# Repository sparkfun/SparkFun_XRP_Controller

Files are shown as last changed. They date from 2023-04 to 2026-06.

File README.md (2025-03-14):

SparkFun XRP Controller
========================================

<table>
    <tr>
        <td></td>
        <td></td>
    </tr>
    <tr>
        <th style="text-align: center;"><a href="https://www.sparkfun.com/sparkfun-experiential-robotics-platform-xrp-controller.html"><i>SparkFun XRP Controller</i></a></th>
        <th style="text-align: center;"><a href="https://www.sparkfun.com/sparkfun-experiential-robotics-platform-xrp-controller-beta.html"><i>SparkFun XRP Controller - Beta</i></a></th>
    </tr>
</table>

The Experiential Robotics Platform (XRP) Controller and Experiential Robotics Platform (XRP) Controller - Beta operate as the "brains" of the Experiential Robotics Platform Kits. These boards provide the programming and operation interface to connect and control the motors, sensors and other peripherals included in the XRP Kits. The controller boards primary microcontrollers are a Pico W (XRP-Beta) and RP2350 (XRP) and also include motor drivers, 6 DoF IMU, motor and sensor connectors along with other user interfaces.

Repository Contents
-------------------

* **/Documents** - Data sheets, additional product information
* **/Hardware** - Eagle design files (.brd, .sch)
* **/Production** - Production panel files (.brd)
* **/docs** - GitHub Pages documentation files (.md, images)

Documentation
--------------

* **[Hardware Overview](https://docs.sparkfun.com/SparkFun_XRP_Controller/introduction/)** - Basic hardware overview for the XRP Controller - Beta and XRP Controller.
* **[Experiential Robotics Platform Org](https://experientialrobotics.org/)** - Experiential Robotics Platform homepage.

Product Versions
----------------

* [ROB-22727](https://www.sparkfun.com/sparkfun-experiential-robotics-platform-xrp-controller-beta.html) - XRP Controller - Beta
* [ROB-26619](https://www.sparkfun.com/sparkfun-experiential-robotics-platform-xrp-controller.html) - XRP Controller

License Information
-------------------

This product is ***open source***!

Please review the LICENSE.md file for license information.

If you have any questions or concerns on licensing, please contact technical support on our [SparkFun forums](https://forum.sparkfun.com/viewforum.php?f=152).

Distributed as-is; no warranty is given.

* Your friends at SparkFun.

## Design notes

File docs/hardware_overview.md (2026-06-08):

In this document, we'll take a close look at the heart of the Experiential Robotics Platform (XRP) Kit, the XRP Controller. This document outlines all of the parts on this board you'll interact with while building and using the XRP Kit.

## Controller Board Overview

Let's take a broad look at the major components on the XRP Controller. The photo below points them out along with their names:

<figure markdown>
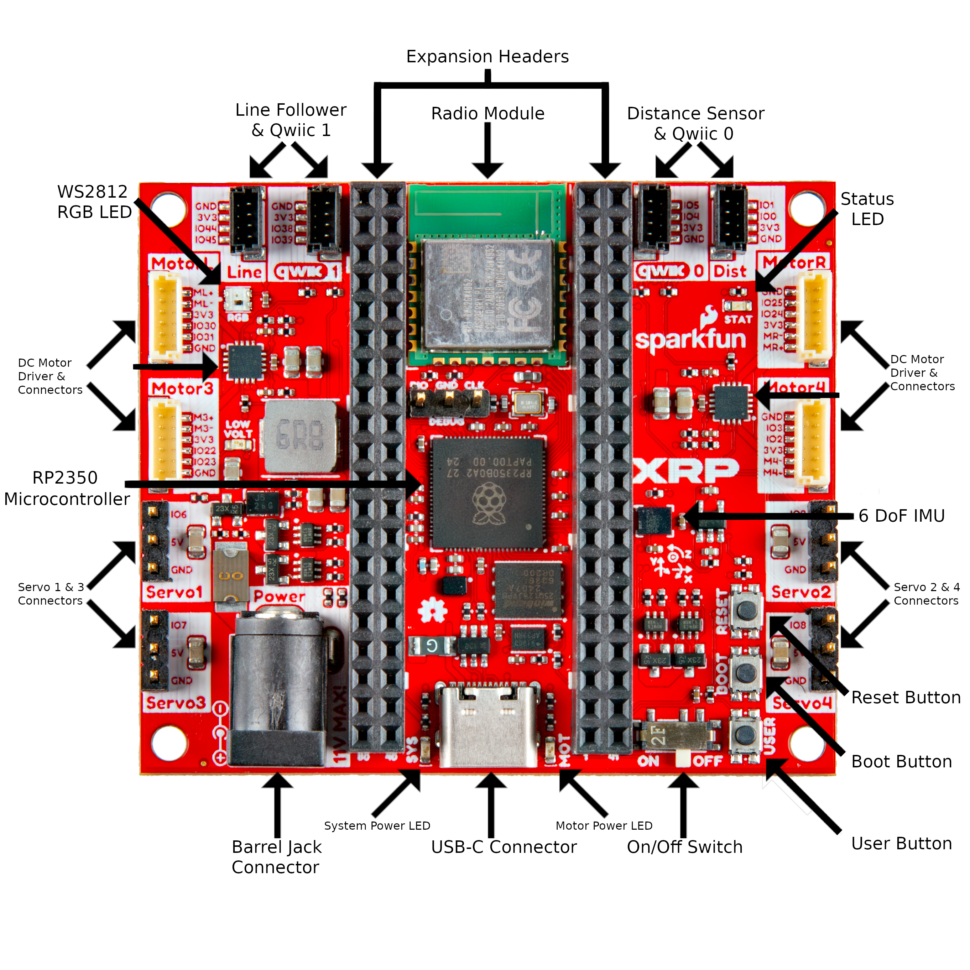
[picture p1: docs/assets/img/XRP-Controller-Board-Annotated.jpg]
Overview photo labeling the major components and other hardware on the XRP Controller Board

<figcaption>Having trouble seeing the detail in the image? Click on it for a larger view.</figcaption>
</figure>

You'll notice that along with the arrows showing the name of some of the smaller components, the board uses what's called silkscreen to label all the connectors, buttons, LEDs and other parts you'll interact with while building and using the XRP Robotics Kit.

## Raspberry Pi RP2350 & Radio Module 2

The Raspberry Pi RP2350 acts as the brain of this board. The RP2350 communicates with the motor controllers, IMU and other components to control the robotics kit's behavior. The Raspberry Pi Radio Module 2 (RM2) adds wireless connectivity to the XRP Controller over both WiFi and Bluetooth<sup>&reg;</sup>. The photo below highlights the RP2350 and RM2 on the Controller Board:

<figure markdown>
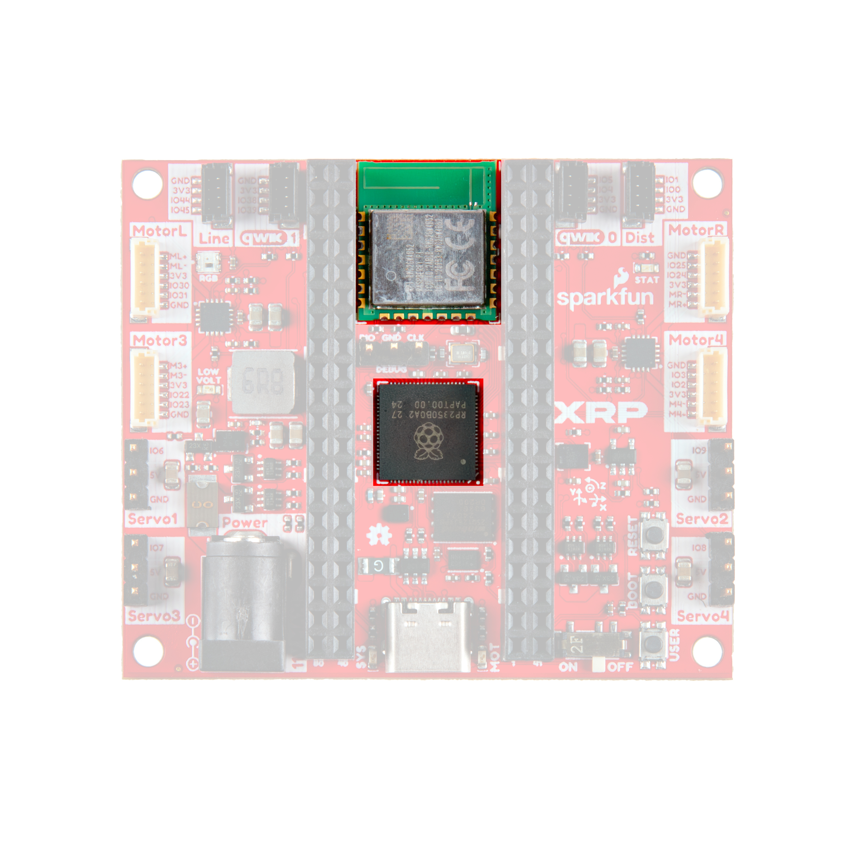
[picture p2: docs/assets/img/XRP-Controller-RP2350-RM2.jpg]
Photo highlighting the RP2350 IC

</figure>

Think of the RP2350 as a brain sending signals to other parts of the "body" to tell them what to do. It has several General Purpose Input/Output (GPIO) pins that connect to the other major parts on this board so it can send and receive data from them and return it to you visually (such as seeing the motors move) or virtually (such as watching data on a computer monitor). 

The Radio Module 2 connects to both WiFi networks and Bluetooth devices allowing wireless connectivity for the XRP Kit. It communicates with the RP2350 over its serial peripheral interface (SPI) and also has a few general purpose inputs and outputs (GPIO) that are connected to the two 2x20 expansion headers on the XRP Controller Board. 

## DRV8411A Motor Drivers

The pair of DRV8411A H-Bridge motor drivers from Texas Instruments<sup>&trade;</sup> on the XRP Controller Board control the direction and speed of the XRP Kit's motors.

<figure markdown>
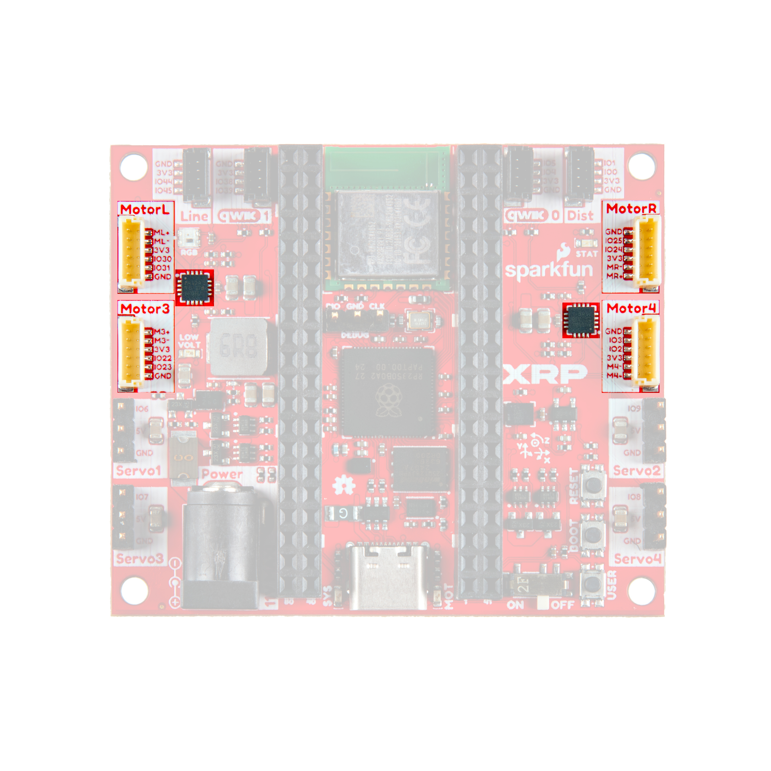
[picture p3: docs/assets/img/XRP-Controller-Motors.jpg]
Photo highlighting the motor drivers.

</figure>

The term H-bridge comes from how this circuit design looks on a schematic diagram. It has four internal switches that control whether the motor spins Clockwise (CW), Counter Clockwise (CCW), Coasts (no drive power), and Stops. When going through the XRP Kit curriculum you'll learn how to program the robot to tell the motor drivers to control the motors' speed and direction.  

## LSM6DSO 6-Dof IMU

The LSM6DSO 6-DoF (Degrees of Freedom) IMU (Inertial Measurement Unit) from STMicroelectronics<sup>&trade;</sup> combines an accelerometer and gyroscope into a single IC (integrated circuit). This sensor lets you measure the robot's acceleration in three dimensions and also measure the orientation and angle of the robot. 

<figure markdown>
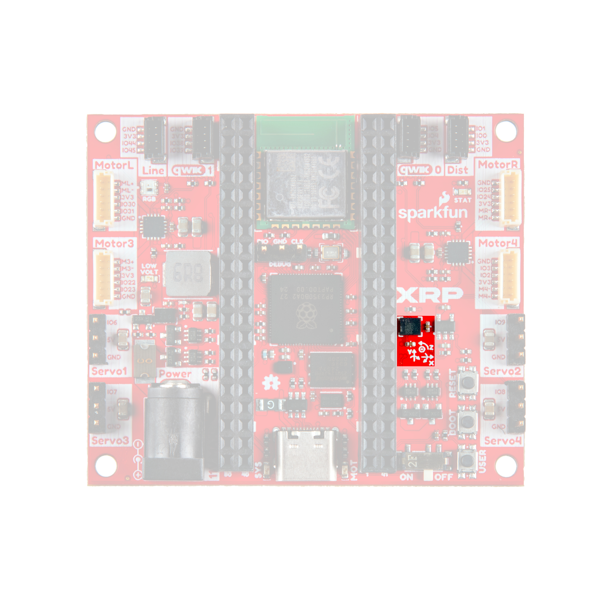
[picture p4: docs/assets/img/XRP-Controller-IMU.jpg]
Photo highlighting the 6 DoF IMU.

</figure>

The accelerometer in this chip has four measurement ranges of &plusmn;2/&plusmn;4/&plusmn;8/&plusmn;16 g. These ranges allow you to customize the limits of the acceleration forces measured. The gyroscope has five selectable measurement ranges of &plusmn;125/&plusmn;250/&plusmn;500/&plusmn;1000/&plusmn;2000 DPS (degrees per second). Refer to the silk screen symbols on the XRP Controller for the directions of each axis.

## Power Components

Now let's take a closer look at the parts on this board used for providing power to it.

<figure markdown>
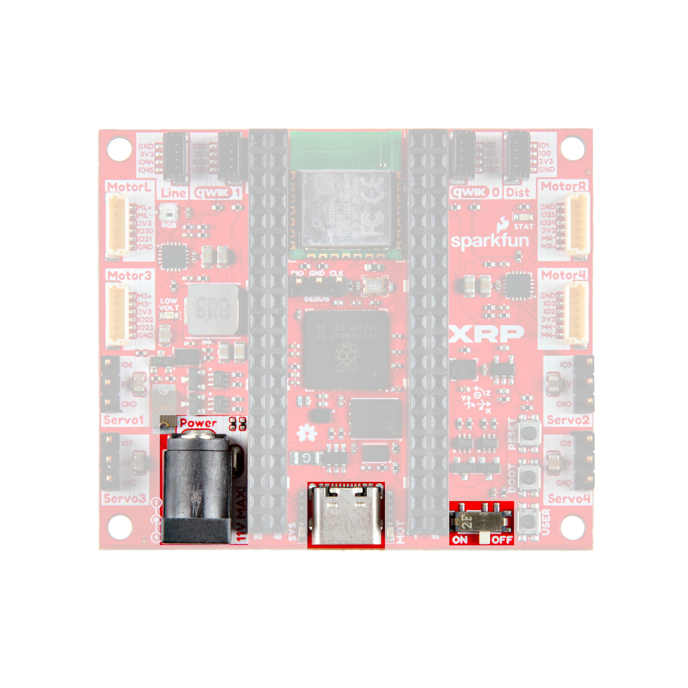
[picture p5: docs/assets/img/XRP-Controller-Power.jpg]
Photo highlighting the power components.

</figure>

### Barrel Jack Connector

The barrel jack connector is the primary power input for the entire XRP Kit. This connector mates with the cable from the XRP Kit's battery pack for battery-powered operation. Take note that the maximum safe voltage that can be applied to this connector is <b>11V</b> and the minimum recommended voltage to run the system is <b>4.8V</b> so you can use non-alkaline batteries like NiMH cells. The 4-AA battery pack included with the kit supplies a maximum of <b>6V</b> so most users will have no issues exceeding the max voltage.

### USB-C Connector

The USB-C connector provides power to the XRP Controller Board with <b>5V</b> from a USB cable. It also is the primary interface you'll use to initially set up the XRP Controller Board with a computer and program the RP2350 using a USB-C cable.

### Power Switch

The power switch highlighted above controls the voltage input to the Controller Board. This two-way switch turns the kit's power on and off. You can use this to turn the robot off while keeping the battery pack plugged in. The switch does not affect the RP2350's power when a USB cable is plugged in.

## Motor Connectors

The Controller Board has four six-pin connectors labeled <b>Motor L</b>, <b>Motor R</b>, <b>Motor 3</b> and <b>Motor 4</b> and four three-pin connectors labeled <b>Servo 1</b>, <b>Servo 2</b>, <b>Servo 3</b> and <b>Servo 4</b>. 

<figure markdown>
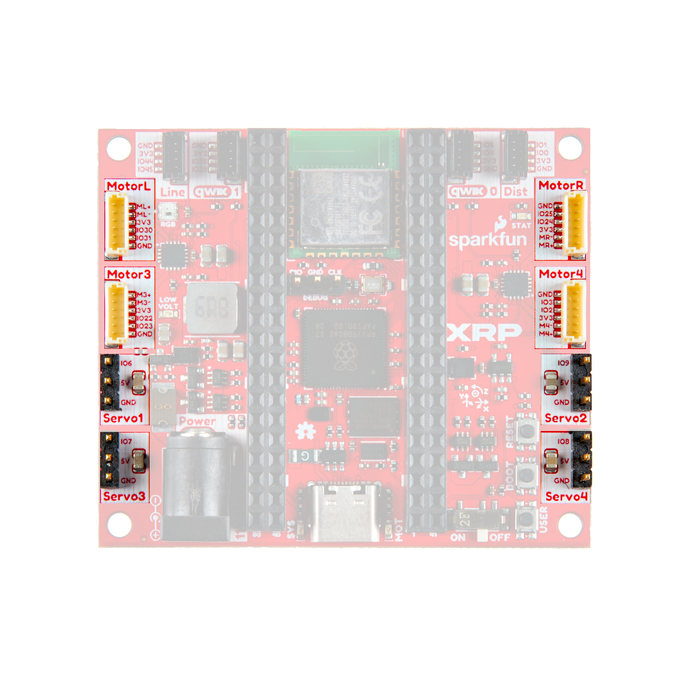
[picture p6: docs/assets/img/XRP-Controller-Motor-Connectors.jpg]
Photo highlighting the motor connectors.

</figure>

### DC Motor Connectors

The DC Motor connectors are where you'll plug in the left and right motors while assembling the kit. These connectors include the power connections for the motor as well as the encoders on the motors. The board routes these connections through the motor drivers to GPIO pins on the RP2350. You'll use these pins to monitor how many rotations the motor completes and use that data to determine how far the robot has traveled. Refer to the Pinout table at the end of this document for the specific GPIO pins each motor connects to on the RP2350. The Controller Board has two extra motor connectors for expansion projects using more than two motors.

### Servo Motor Connectors

The four three-pin connectors on either side of the board labeled Servo 1, Servo 2, Servo 3 and Servo 4 mate with servo motors. You'll use the Servo 2 connector to hook up the servo included in the XRP kit. The other three connectors are extra for expansion projects. These connectors have power pins (<b>5V</b> and Ground) and a signal pin to control the motion of the servo motor. Servo motors use a communication method called pulse width modulation (PWM) that tells the motor to move and with some motors, where to move to. If you're interested in learning more about how servo motors work, you may want to check out SparkFun's [Servos Explained](https://www.sparkfun.com/servos) page for information and tutorials on how to use them.

## Sensor & Qwiic Connectors

The Controller Board has four four-pin connectors labeled (from left to right when looking at the labels upright) <b>Line</b>, <b>Qwiic 1</b>, <b>Qwiic 0</b> and <b>DIST</b>. Their labels indicate their use as well as which GPIO pins they connect to on the RP2350. These connectors provide an easy plug-in connection for the line follower and distance sensor as well as two extra connectors for expansion projects. These connectors are polarized meaning they only work when connected properly but they are keyed and there is only one way to plug a cable into them.

<figure markdown>
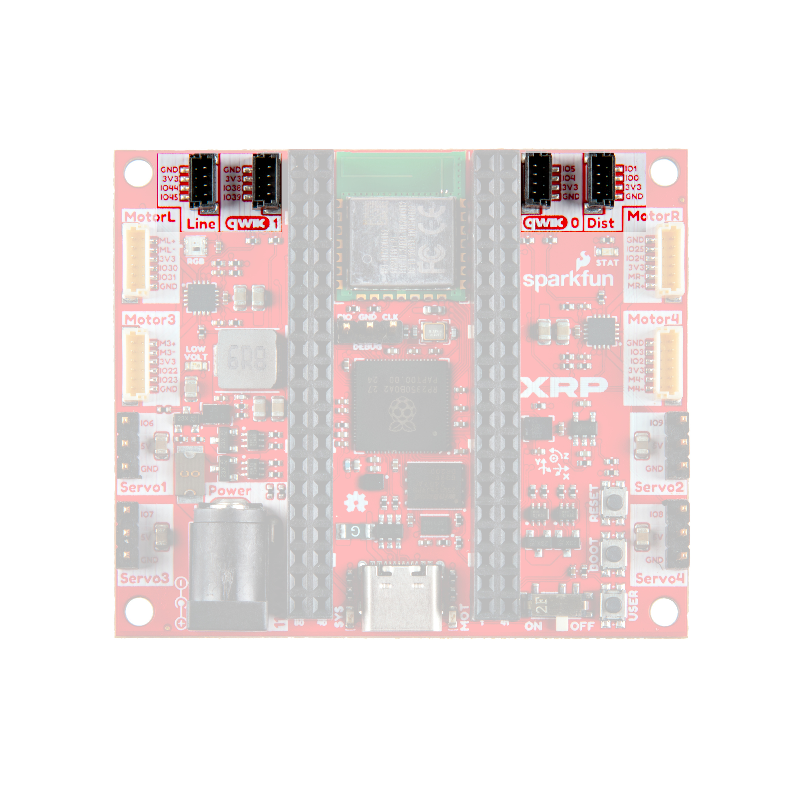
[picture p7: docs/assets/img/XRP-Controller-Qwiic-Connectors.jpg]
Photo highlighting Qwiic and expansion connectors

</figure>

### Line Follower Connector

The Line connector is where you'll plug the cable for the line follower sensor into. This connects the sensor's two signal lines, Left and Right, to the RP2350's GPIO44 (Left) and GPIO45 (Right) pins. You'll use these pins to monitor whenever the sensor detects the robot has gone past the left or right threshold when performing line-following experiments. When connecting the Qwiic adapter cable that plugs into this connector, make the following connections to the Line Follower Sensor:

* **Red** - **3.3V**
* **Blue** - **S1**
* **Yellow** - **S2**
* **Black** - **GND**

### Distance Sensor Connector

The Dist connector is where you'll plug the cable for the ultrasonic range sensor into. It connects the distance sensor's Echo and Trigger lines to the RP2350's GPIO0 (Trigger) and GPIO1 (Echo). You'll use these pins to receive distance data from the ultrasonic range sensor. When connecting the Qwiic adapter cable that plugs into this connector, make the following connections to the Distance Sensor:

* **Red** - **VCC**
* **Blue** - **Trig**
* **Yellow** - **Echo**
* **Black** - **GND**

### Qwiic Connectors

The Qwiic connectors work with SparkFun's [Qwiic ecosystem](https://www.sparkfun.com/qwiic) of sensors that communicate over I<sup>2</sup>C. This is a two-wire communication protocol that works with a large variety of sensors and other electronics. With this, you can customize the XRP Kit to add things like environmental sensing, OLED screens, data logging, and more!

## Buttons

The Controller Board has three push buttons labeled <b>USER</b>, <b>RESET</b> and <b>BOOT</b> (on the RP2350). 

<figure markdown>
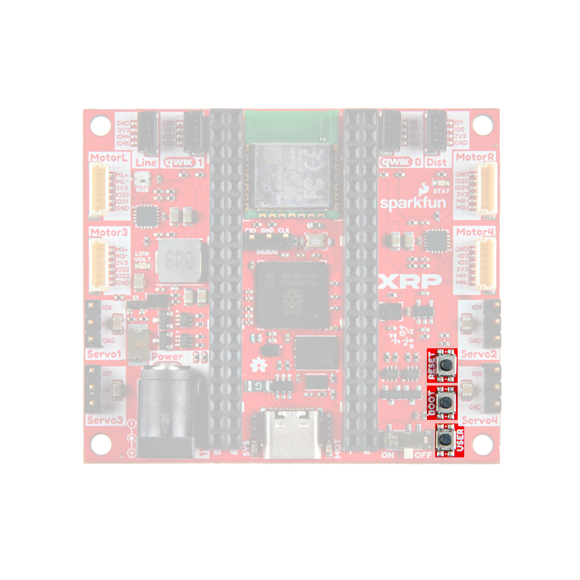
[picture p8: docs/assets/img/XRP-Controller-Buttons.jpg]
Photo highlighting buttons.

</figure>

The USER button connects to GPIO36 on the RP2350 which allows it to be programmed for various purposes. The RESET button does just what its name suggests and resets the entire board when pressed. This can help to reboot the robot or to restart a sequence you want the Robotics Kit to perform. Holding the BOOT button either when plugging in a USB cable or when pressing the RESET button sets the RP2350 to behave as a mass storage device when connected to a computer for uploading firmware. 

## LEDs

There are five LEDs on the XRP Controller Board labeled <b>MOT</b>, <b>SYS</b>, <b>LOW VOLT</b>, <b>STAT</b> and <b>RGB</b>. 

<figure markdown>
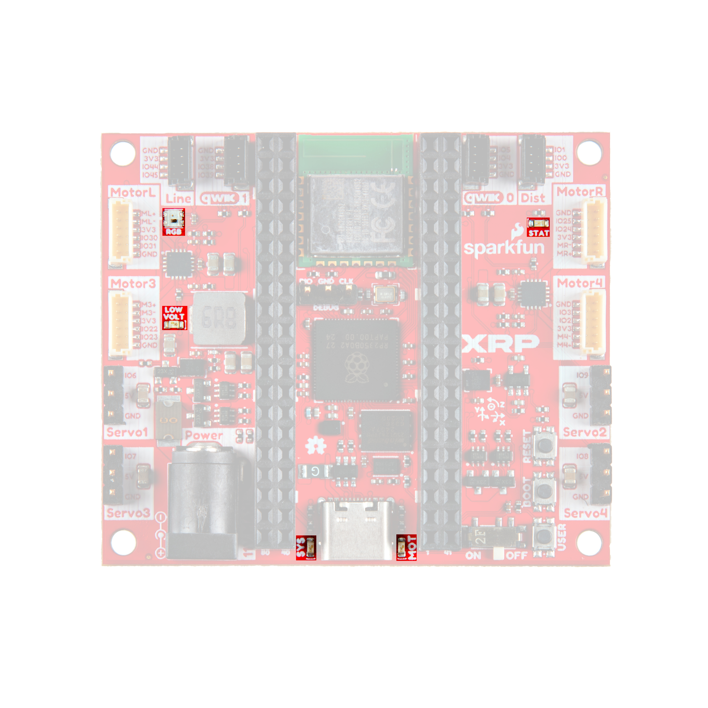
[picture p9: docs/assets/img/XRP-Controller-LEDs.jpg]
Photo highlighting LEDs

</figure>

These LEDs are there to provide a visual indication to users. The LEDs labeled <b>MOT</b> and <b>SYS</b> turn on when their respective power rails are powered. The <b>MOT</b> LED turns on when the motors have power available. The <b>SYS</b> LED turns on when the <b>3.3V</b>/System circuit is powered. This circuit powers the RP2350, RM2, sensors, and the expansion connectors. The <b>LOW VOLT</b> LED connects to the 5V Buck regulator POWER_GOOD pin. It provides a quick visual indicator to notify users that the supply voltage has dropped below the operating threshold and the board is underpowered. This is <b>not</b> technically a low battery indicator but it coincidentally starts illuminating when 4xAA batterys are low, depending on the battery chemistry. 

The other two LEDs labeled <b>STAT</b> and <b>RGB</b> are user-programmable status LEDs you can program for whatever behavior you prefer. The <b>STAT</b> LED connects to GPIO0 on the Radio Module and can be useful to indicate behavior from the radio such as connection status or data transmission. The <b>RGB</b> LED connects to GPIO37 on the RP2350 and can be programmed to change to any color based on whatever behavior you'd like. For example, you can have it turn from Green to Red when the distance sensor detects the robot is nearing an obstacle. 

## Expansion Headers

The XRP Controller Board now features a pair of 2x20 female headers that connect to nearly all the RP2350's and RM2's available pins to allow for more customization options for the XRP platform. Many of these pins are shared between the connectors and other components on the XRP Control Board so take care to ensure they are not being used by any peripherals (motors, sensors, etc.) before connecting and programming them for a different functionality.

<figure markdown>
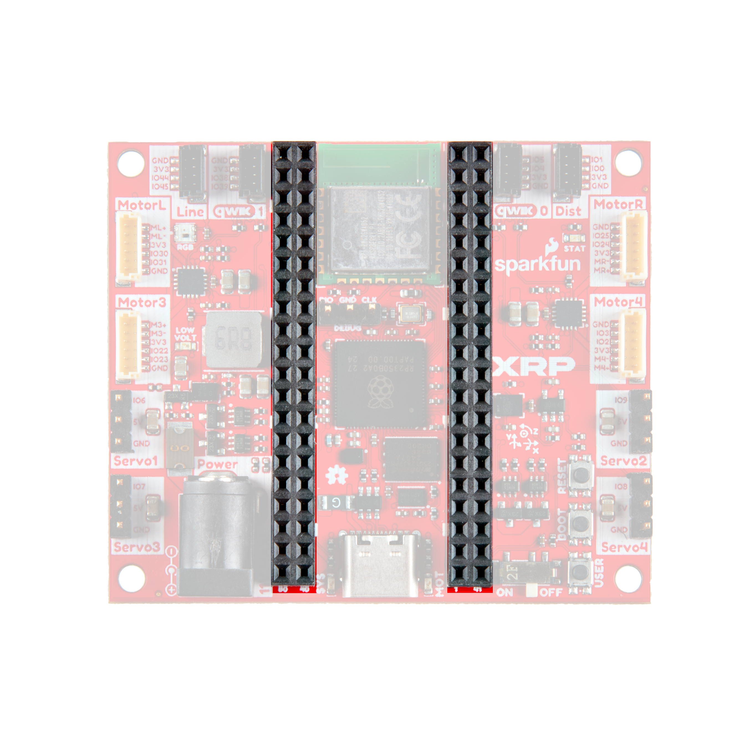
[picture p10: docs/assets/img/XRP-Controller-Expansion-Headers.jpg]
Photo highlighting 2x20 expansion headers.

</figure>

The inner rows of this expansion header nearly matches the pinout of the Pico W 2 (minus the analog-to-digital conversion pins) and can be used with peripheral boards that work with the Pico 2 W. Please note this is <b>NOT</b> a socket for a Pico 2 W. The outer row contains available GPIO pins from the RM2, extra GPIO pins from the RP2350 along with voltage pins. The image below and following table offers a quick reference for the pinout and labels on the expansion headers as well as any other connectors (motors, sensors, etc.) or peripheral (button, LED, etc.) shared between them.

<figure markdown>
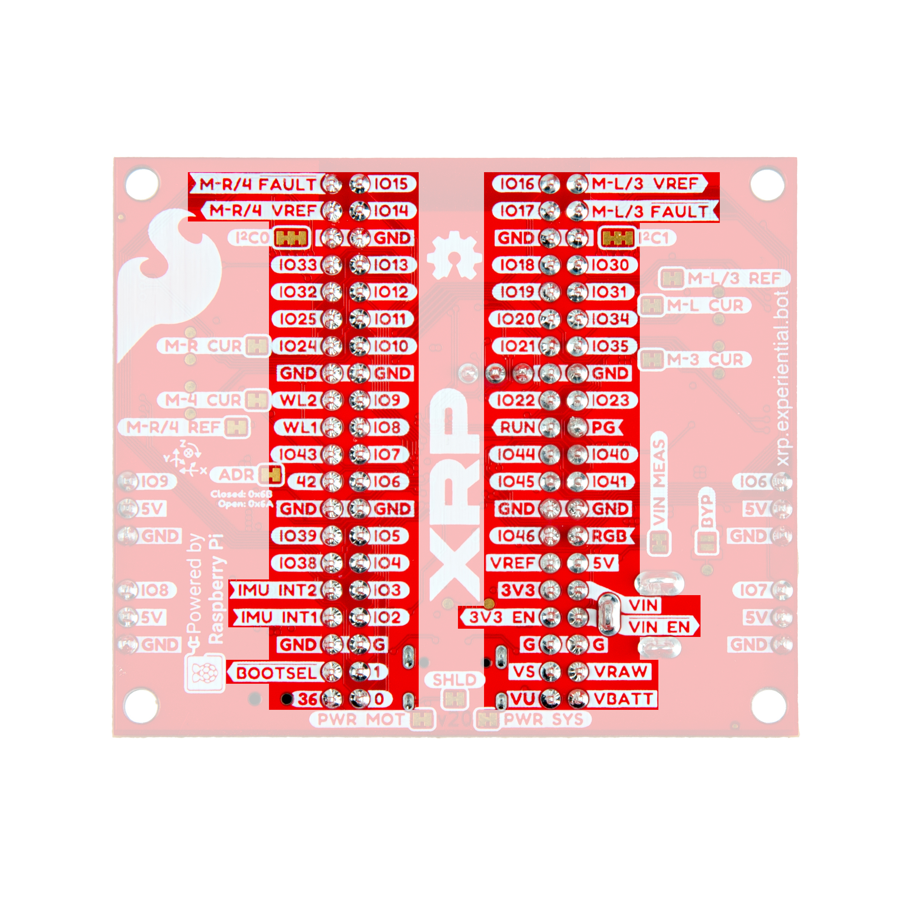
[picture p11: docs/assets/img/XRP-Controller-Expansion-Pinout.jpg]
Photo highlighting pin labels on the XRP Controller board.

</figure> 

<figure markdown>
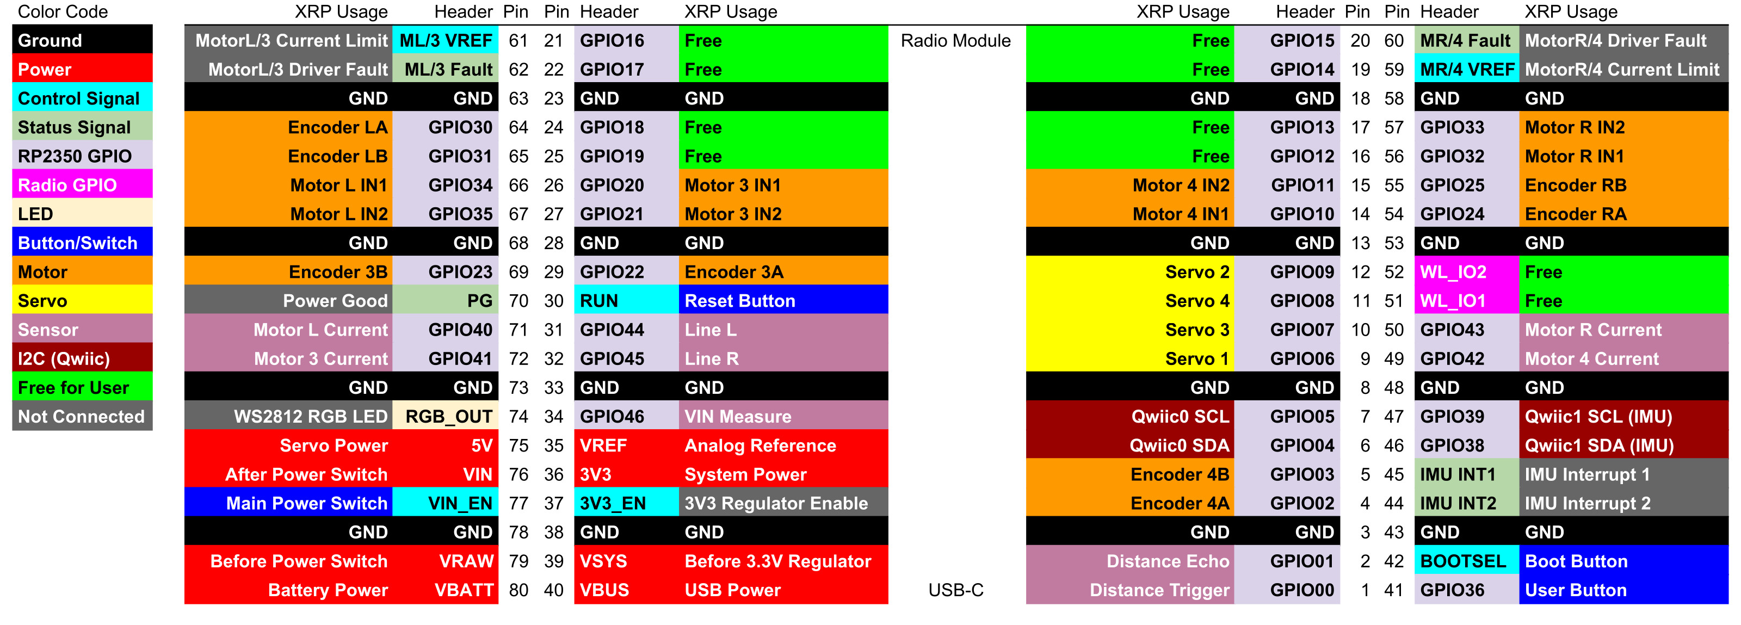
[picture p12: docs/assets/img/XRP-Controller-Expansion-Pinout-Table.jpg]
Table of expansion header pinout

</figure>

## Solder Jumpers

!!! warning Advanced Users Only

    These solder jumpers can change the behavior of the board in a lasting way. Using these requires extra tools not included in the XRP
     Kit along with knowledge of how to use and interact with solder jumpers. We recommend that only advanced users adjust and change the solder jumpers. If you'd like to learn more about how to use solder jumpers, check out SparkFun's [How to Work with Jumper Pads and PCB Traces](https://learn.sparkfun.com/tutorials/how-to-work-with-jumper-pads-and-pcb-traces) tutorial.

The XRP Controller Board has fourteen solder jumpers. A solder jumper provides a customization option for advanced users to control the behavior of the pins and components they connect to. The solder jumpers on this board are labeled (from top-to-bottom reading left-to-right when looking at the photo below): <b>I<sup>2</sup>C0</b>, <b>I<sup>2</sup>C1</b>, <b>M-L/3 REF</b>, <b>M-L CUR</b>, <b>M-R CUR</b>, <b>M-3 CUR</b>, <b>M-4 CUR</b>, <b>M-R/4 REF</b> <b>ADR</b>, <b>VIN MEAS</b>, <b>BYPM</b>, <b>SHLD</b>, <b>PWR MOT</b> and <b>PWR SYS</b>. 

<figure markdown>
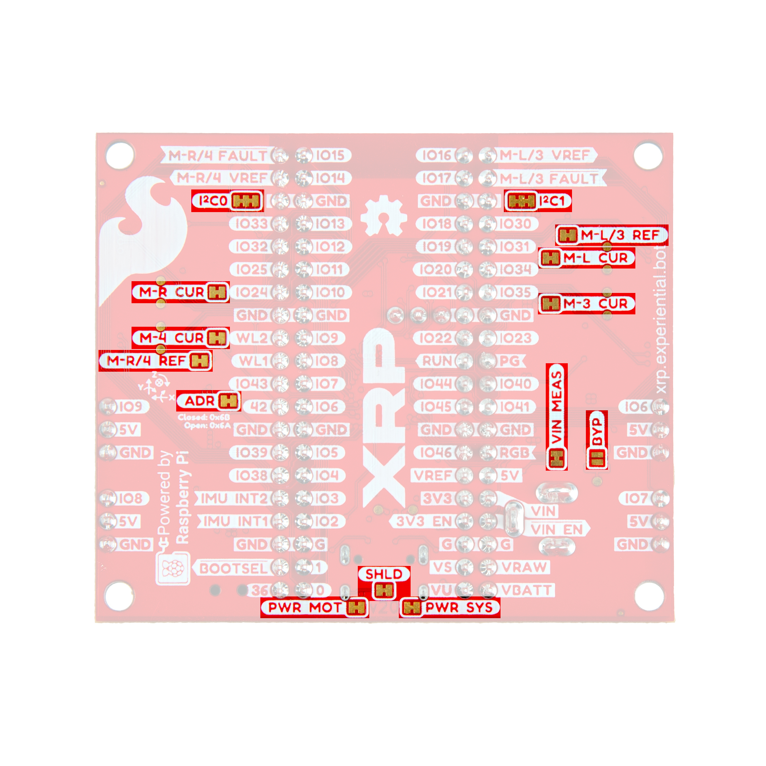
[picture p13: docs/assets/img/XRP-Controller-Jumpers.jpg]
Photo highlighting solder jumpers.

</figure>

<table>
    <tr>
        <th>Label</th>
        <th>Default State</th>
        <th>Function</th>
        <th>Notes</th>
    </tr>
    <tr>
        <td>I<sup>2</sup>C0</td>
        <td>CLOSED</td>
        <td>Pulls SDA/SCL on I<sup>2</sup>C 0 to <b>3.3V</b> through two <b>2.2k&ohm;</b> resistors.</td>
        <td>Open completely to disable the pull up resistors on the I<sup>2</sup>C 0 bus.</td>
    </tr>
    <tr>
        <td>I<sup>2</sup>C1</td>
        <td>CLOSED</td>
        <td>Pulls SDA/SCL on I<sup>2</sup>C 0 to <b>3.3V</b> through two <b>2.2k&ohm;</b> resistors.</td>
        <td>Open completely to disable the pull up resistors on the I<sup>2</sup>C 1 bus.</td>
    </tr>
    <tr>
        <td>M-L/3 REF</td>
        <td>CLOSED</td>
        <td>Sets the Left/3 DRV8411 motor driver's voltage reference to <b>3.3V</b.</td>
        <td>Sets the DRV8411's reference voltage to match the system voltage. Open to set to a different voltage.</td>
    </tr>
    <tr>
        <td>M-L CUR</td>
        <td>CLOSED</td>
        <td>Connects the Left Motor current sense output to IO40.</td>
        <td>Lets users measure motor current draw using the ADC on IO40. Open to free up IO40 for other use.</td>
    </tr>
    <tr>
        <td>M-R CUR</td>
        <td>CLOSED</td>
        <td>Connects the Right Motor current sense output to IO43.</td>
        <td>Lets users measure motor current draw using the ADC on IO43. Open to free up IO43 for other use.</td>
    </tr>
    <tr>
        <td>M-3 CUR</td>
        <td>CLOSED</td>
        <td>Connects the Motor Three current senss output to IO41.</td>
        <td>Lets users measure motor current draw using the ADC on IO41. Open to free up IO41 for other use.</td>
    </tr>
    <tr>
        <td>M-4 CUR</td>
        <td>CLOSED</td>
        <td>Connects the Motor Four current sense output to IO42.</td>
        <td>Lets users measure motor current draw using the ADC on IO42. Open to free up IO42 for other use.</td>
    </tr>
    <tr>
        <td>M-R/4 REF</td>
        <td>CLOSED</td>
        <td>Sets the Right/4 DRV8411 motor driver's voltage reference to <b>3.3V</b.</td>
        <td>This sets the DRV8411's reference voltage to match the system voltage. Open to set to a different voltage.</td>
    </tr>
    <tr>
        <td>ADR</td>
        <td>CLOSED</td>
        <td>Sets the LSM6DSO's I<sup>2</sup>C address to <b>0x6B</b>.</td>
        <td>Open to switch the I<sup>2</sup>C address to <b>0x6A</b>.</td>
    </tr>
    <tr>
        <td>VIN MEAS</td>
        <td>CLOSED</td>
        <td>Connects the VIN measurement circuit to IO46</td>
        <td>Open to free up IO46 for alternate use</td>
    </tr>
    <tr>
        <td>BYP</td>
        <td>OPEN</td>
        <td>Enables the fuse for the barrel jack input.</td>
        <td>Close to bypass the fuse for the barrel jack.</td>
    </tr>
    <tr>
        <td>SHLD</td>
        <td>CLOSED</td>
        <td>Connects the USB-C shield pin to the board's ground plane.</td>
        <td>Open to isolate the USB-C shield pin</td>
    </tr>
    <tr>
        <td>PWR MOT</td>
        <td>CLOSED</td>
        <td>Completes the Motor Power LED circuit.</td>
        <td>Open to disable the Motor Power LED.</td>
    </tr>
    <tr>
        <td>PWR SYS</td>
        <td>CLOSED</td>
        <td>Completes the System Power LED circuit.</td>
        <td>Open to disable the System Power LED.</td>
    </tr>
</table>

## Pinout Reference Table

The table below gives a quick reference for the complete pinout of the XRP Controller and which pins they connect to on the RP2350.

<table>
    <tr>
        <th>RP2350 GPIO Pin</th>
        <th>Connector/Peripheral Label</th>
        <th>Expansion Header Pin Label</th>
        <th>Pin Function</th>
    </tr>
    <tr>
        <td>GPIO0</td>
        <td>DIST</td>
        <td>0</td>
        <td>Distance Trigger Pin</td>
    </tr>
    <tr>
        <td>GPIO1</td>
        <td>DIST</td>
        <td>1</td>
        <td>Distance Echo Pin</td>
    </tr>
    <tr>
        <td>GPIO2</td>
        <td>Motor 4</td>
        <td>IO2</td>
        <td>Motor 4 Encoder A</td>
    </tr>
    <tr>
        <td>GPIO3</td>
        <td>Motor 4</td>
        <td>IO3</td>
        <td>Motor 4 Encoder B</td>
    </tr>
    <tr>
        <td>GPIO4</td>
        <td>Qwiic 0</td>
        <td>IO4</td>
        <td>I<sup>2</sup>C 0 Data Signal</td>
    </tr>
    <tr>
        <td>GPIO5</td>
        <td>Qwiic 0</td>
        <td>IO5</td>
        <td>I<sup>2</sup>C 0 Clock</td>
    </tr>
    <tr>
        <td>GPIO6</td>
        <td>Servo 1</td>
        <td>IO6</td>
        <td>Servo 1 Signal</td>
    </tr>
    <tr>
        <td>GPIO7</td>
        <td>Servo 3</td>
        <td>IO7</td>
        <td>Servo 3 Signal</td>
    </tr>
    <tr>
        <td>GPIO8</td>
        <td>Servo 4</td>
        <td>IO8</td>
        <td>Servo 4 Signal</td>
    </tr>
    <tr>
        <td>GPIO9</td>
        <td>Servo 2</td>
        <td>IO9</td>
        <td>Servo 2 Signal</td>
    </tr>
    <tr>
        <td>GPIO10</td>
        <td>Motor 4</td>
        <td>IO10</td>
        <td>Motor 4 Phase Pin</td>
    </tr>
    <tr>
        <td>GPIO11</td>
        <td>Motor 4</td>
        <td>IO11</td>
        <td>Motor 4 Enable Pin</td>
    </tr>
    <tr>
        <td>GPIO12</td>
        <td>None</td>
        <td>IO12</td>
        <td>Available I/O</td>
    </tr>
    <tr>
        <td>GPIO13</td>
        <td>None</td>
        <td>IO13</td>
        <td>Available I/O</td>
    </tr>
    <tr>
        <td>GPIO14</td>
        <td>None</td>
        <td>IO14</td>
        <td>Available I/O</td>
    </tr>
    <tr>
        <td>GPIO15</td>
        <td>None</td>
        <td>IO15</td>
        <td>Available I/O</td>
    </tr>
    <tr>
        <td>GPIO16</td>
        <td>None</td>
        <td>IO16</td>
        <td>Available I/O</td>
    </tr>
    <tr>
        <td>GPIO17</td>
        <td>None</td>
        <td>IO17</td>
        <td>Available I/O</td>
    </tr>
    <tr>
        <td>GPIO18</td>
        <td>None</td>
        <td>IO18</td>
        <td>Available I/O</td>
    </tr>
    <tr>
        <td>GPIO19</td>
        <td>None</td>
        <td>IO19</td>
        <td>Available I/O</td>
    </tr>
    <tr>
        <td>GPIO20</td>
        <td>Motor 3</td>
        <td>IO20</td>
        <td>Motor 3 Phase Pin</td>
    </tr>
    <tr>
        <td>GPIO21</td>
        <td>Motor 3</td>
        <td>IO21</td>
        <td>Motor 3 Enable Pin</td>
    </tr>
    <tr>
        <td>GPIO22</td>
        <td>Motor 3</td>
        <td>IO22</td>
        <td>Motor 3 Encoder A Pin</td>
    </tr>
    <tr>
        <td>GPIO23</td>
        <td>Motor 3</td>
        <td>IO23</td>
        <td>Motor 3 Encoder B Pin</td>
    </tr>
    <tr>
        <td>GPIO24</td>
        <td>Motor R</td>
        <td>IO24</td>
        <td>Motor R Encoder A Pin</td>
    </tr>
    <tr>
        <td>GPIO25</td>
        <td>Motor R</td>
        <td>IO25</td>
        <td>Motor R Encoder B Pin</td>
    </tr>
    <tr>
        <td>GPIO26</td>
        <td>None</td>
        <td>None</td>
        <td>RM2 Power On</td>
    </tr>
        <td>GPIO27</td>
        <td>None</td>
        <td>None</td>
        <td>RM2 Chip Select</td>
    </tr>
    </tr>
        <td>GPIO28</td>
        <td>None</td>
        <td>None</td>
        <td>RM2 SPI Clock</td>
    </tr>
    </tr>
        <td>GPIO29</td>
        <td>None</td>
        <td>None</td>
        <td>RM2 SPI Data</td>
    </tr>
    <tr>
        <td>GPIO30</td>
        <td>Motor L</td>
        <td>IO30</td>
        <td>Motor L Encoder A Pin</td>
    </tr>
    <tr>
        <td>GPIO31</td>
        <td>Motor L</td>
        <td>IO31</td>
        <td>Motor L Encoder B Pin</td>
    </tr>
    <tr>
        <td>GPIO32</td>
        <td>Motor R</td>
        <td>IO32</td>
        <td>Motor R Phase Pin</td>
    </tr>
    <tr>
        <td>GPIO33</td>
        <td>Motor R</td>
        <td>IO33</td>
        <td>Motor R Enable Pin</td>
    </tr>
    <tr>
        <td>GPIO34</td>
        <td>Motor L</td>
        <td>IO34</td>
        <td>Motor L Phase Pin</td>
    </tr>
    <tr>
        <td>GPIO35</td>
        <td>Motor L</td>
        <td>IO35</td>
        <td>Motor L Enable Pin</td>
    <tr>
    <tr>
        <td>GPIO36</td>
        <td>User Button</td>
        <td>36</td>
        <td>User button input</td>
    </tr>
    <tr>
        <td>GPIO37</td>
        <td>RGB</td>
        <td>RGB</td>
        <td>WS2812 Data In Pin</td>
    </tr>
    <tr>
        <td>GPIO38</td>
        <td>Qwiic 1</td>
        <td>SDA1</td>
        <td>I<sup>2</sup>C 1 Data</td>
    </tr>
    <tr>
        <td>GPIO39</td>
        <td>Qwiic 1</td>
        <td>SCL1</td>
        <td>I<sup>2</sup>C 1 Clock</td>
    </tr>
    <tr>
        <td>GPIO40</td>
        <td>None</td>
        <td>IO40</td>
        <td>Motor Left Current Measure</td>
    </tr>
    <tr>
        <td>GPIO41</td>
        <td>None</td>
        <td>IO41</td>
        <td>Motor 3 Current Measure</td>
    </tr>
    <tr>
        <td>GPIO42</td>
        <td>None</td>
        <td>IO42</td>
        <td>Motor 4 Current Measure</td>
    </tr>
    <tr>
        <td>GPIO43</td>
        <td>None</td>
        <td>IO43</td>
        <td>Motor Right Current Measure</td>
    </tr>
    <tr>
        <td>GPIO44</td>
        <td>Line</td>
        <td>IO44</td>
        <td>Line Follower Left Signal</td>
    </tr>
    <tr>
        <td>GPIO45</td>
        <td>Line</td>
        <td>IO45</td>
        <td>Line Follower Right Signal</td>
    </tr>
    <tr>
        <td>GPIO46</td>
        <td>None</td>
        <td>IO46</td>
        <td>Voltage Input Measure</td>
    </tr>
    <tr>
        <td>GPIO47</td>
        <td>None</td>
        <td>None</td>
        <td>PSRAM Chip Select</td>
    </tr>
</table>

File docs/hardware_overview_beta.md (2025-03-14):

In this document, we'll take a close look at the heart of the Experiential Robotics Platform (XRP) Kit - Beta, the XRP Controller - Beta. This document outlines all of the parts on this board you'll interact with while building and using the XRP Kit - Beta.

## XRP Controller - Beta Overview

Let's take a broad look at the major components on the XRP Controller - Beta. The photo below points them out along with their names:

<figure markdown>
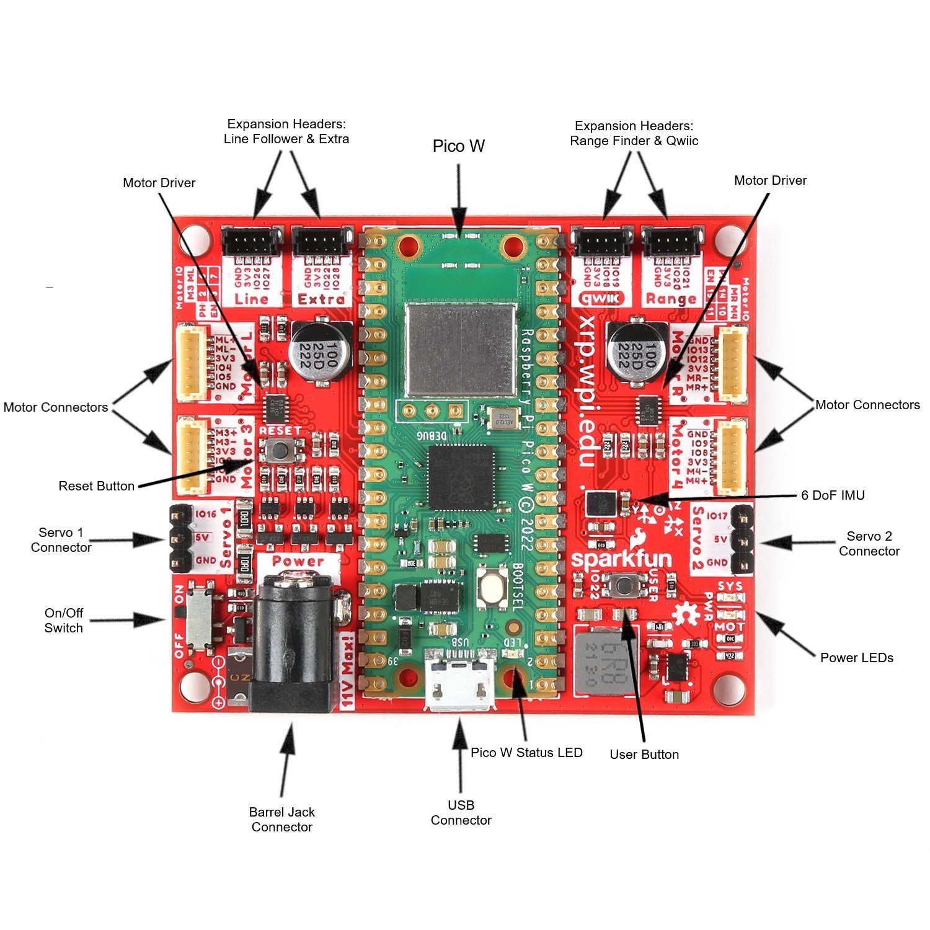
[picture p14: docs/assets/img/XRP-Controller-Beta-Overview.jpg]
Overview photo labeling the major components and other hardware on the XRP Controller - Beta

<figcaption>Having trouble seeing the detail in the image? Click on it for a larger view.</figcaption>
</figure>

You'll notice that along with the arrows showing the name of some of the smaller components, the board uses what's called silkscreen to label all the connectors, buttons, LEDs and other parts you'll interact with while building and using the XRP Kit - Beta.

## Raspberry Pi Pico W

The Raspberry Pi Pico W microcontroller acts as the brain of this board. It combines a RP2040 processor with a wireless module for both 2.4GHz 802.11n wireless LAN and Bluetooth<sup>&trade;</sup> 5.2. The RP2040 communicates with the motor controllers, IMU and other components to control the robotics kit's behavior. The photo below highlights the Pico W on the Controller board:

<figure markdown>
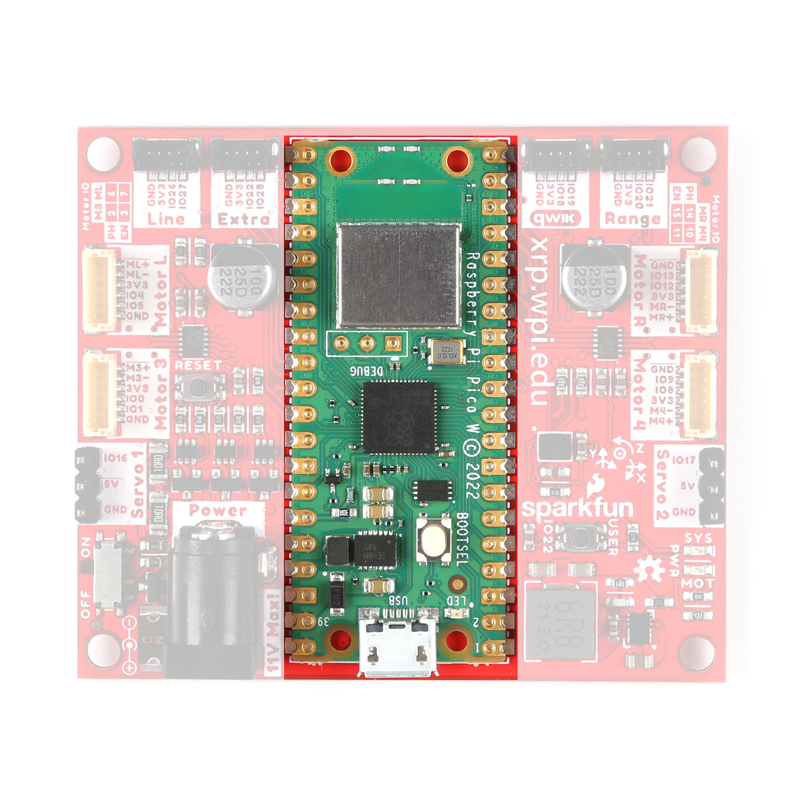
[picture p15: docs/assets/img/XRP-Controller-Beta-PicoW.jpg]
Photo highlighting the Pico W microcontroller

</figure>

Think of the Pico W as a brain sending signals to other parts of the "body" to tell them what to do. It has several General Purpose Input/Output (GPIO) pins that connect to the other major parts on this board so it can send and receive data from them and return it to you visually (such as seeing the motors move) or virtually (such as watching data on a computer monitor). 

## DRV8835 Motor Drivers

The pair of DRV8835 H-Bridge motor drivers from Texas Instruments<sup>&trade;</sup> on the XRP Controller - Beta control the direction and speed of the Robotics Kit's motors.

<figure markdown>
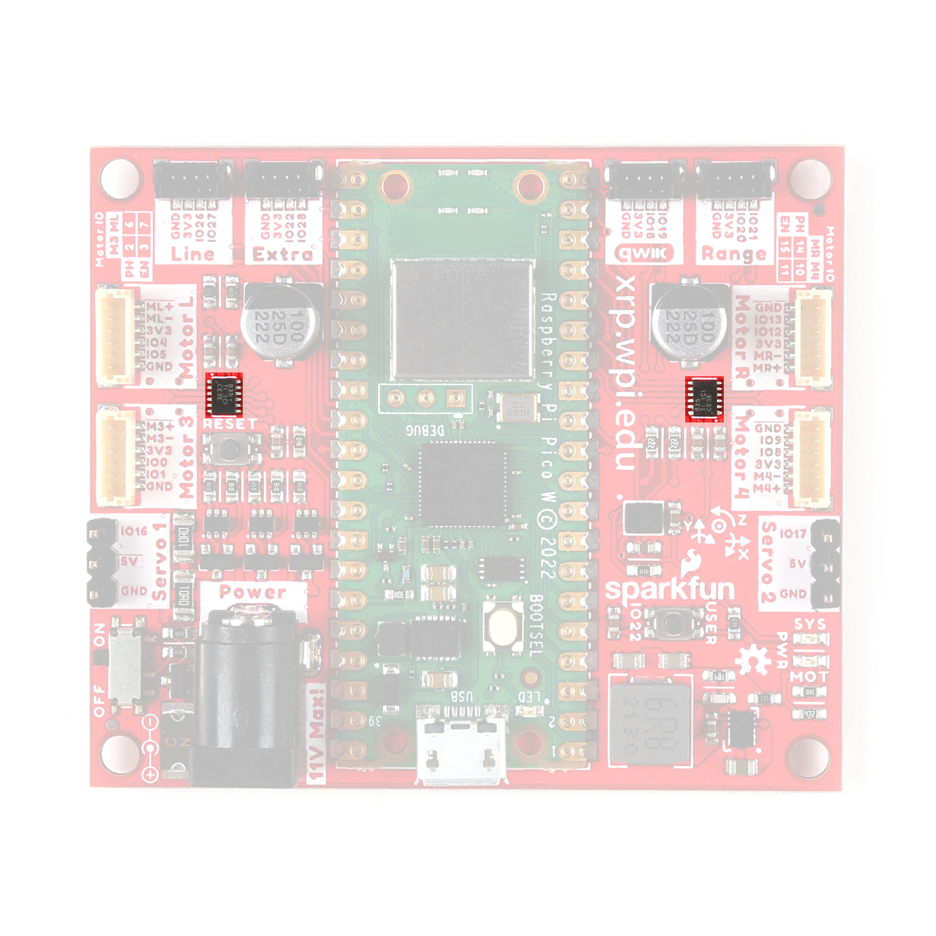
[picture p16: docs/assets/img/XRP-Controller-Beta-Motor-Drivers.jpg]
Photo highlighting the motor drivers.

</figure>

The term H-bridge comes from how this circuit design looks on a schematic diagram. It has four internal switches that control whether the motor spins Clockwise (CW), Counter Clockwise (CCW), Coasts (no drive power), and Stops. When going through the XRP Kit - Beta curriculum you'll learn how to program the robot to tell the motor drivers to control the motors' speed and direction.  

## LSM6DSO 6-Dof IMU

The LSM6DSO 6-DoF (Degrees of Freedom) IMU (Inertial Measurement Unit) from STMicroelectronics<sup>&trade;</sup> combines an accelerometer and gyroscope into a single IC (integrated circuit). This sensor lets you measure the robot's acceleration in three dimensions and also measure the orientation and angle of the robot. 

<figure markdown>
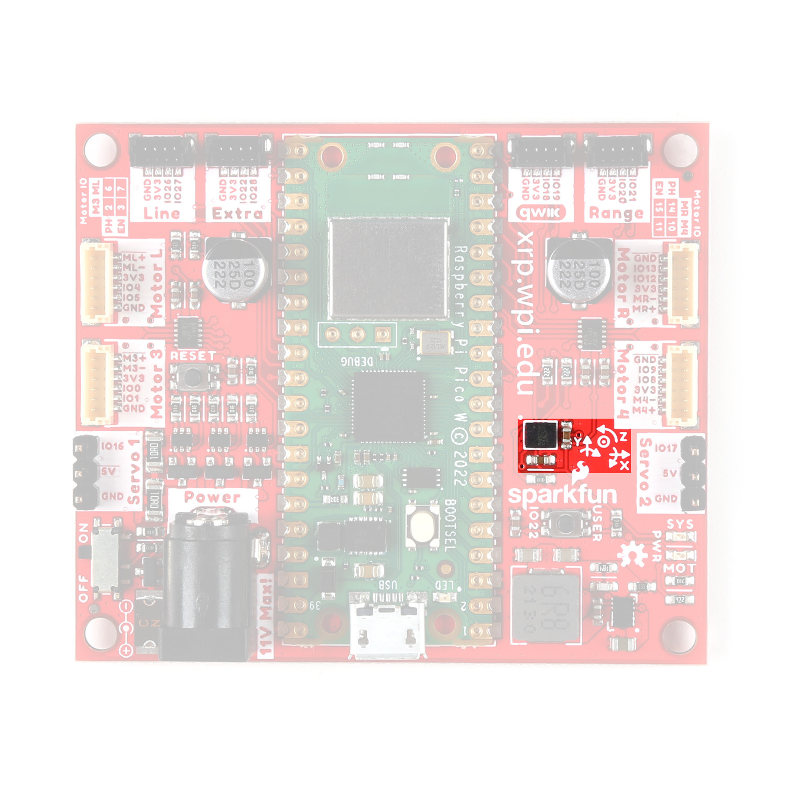
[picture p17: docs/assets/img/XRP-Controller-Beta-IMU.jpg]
Photo highlighting the 6 DoF IMU.

</figure>

The accelerometer in this chip has four measurement ranges of &plusmn;2/&plusmn;4/&plusmn;8/&plusmn;16 g. These ranges allow you to customize the limits of the acceleration forces measured. The gyroscope has five selectable measurement ranges of &plusmn;125/&plusmn;250/&plusmn;500/&plusmn;1000/&plusmn;2000 DPS (degrees per second).

## Power Components

Now let's take a closer look at the parts on this board used for providing power to it.

<figure markdown>
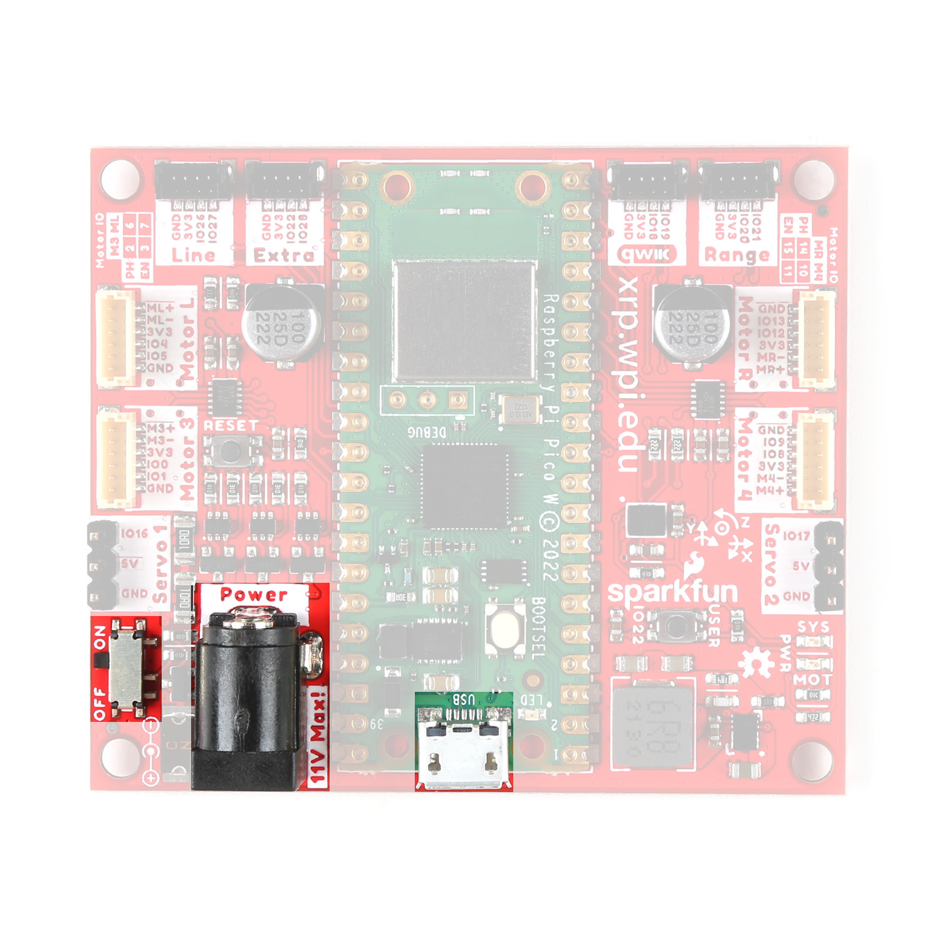
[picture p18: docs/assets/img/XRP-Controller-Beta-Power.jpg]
Photo highlighting the power components.

</figure>

### Barrel Jack Connector

The barrel jack connector is the primary power input for the entire XRP Kit - Beta. This connector mates with the cable from the XRP Kit - Beta's battery pack for battery-powered operation. Take note that the maximum safe voltage that can be applied to this connector is <b>11V</b> and the minimum to run the system is <b>5V</b>. The 4-AA battery pack included with the kit supplies a maximum of <b>6V</b> so most users will have no issues exceeding the max voltage.

### Pico W USB-Connector

The Pico W has a Micro-USB connector that can be used to power the controller board with <b>5V</b> from a USB cable. It also is the primary interface you'll use to initially set up the Pico W with a computer and program the Pico W over a USB cable.

### Power Switch

The power switch highlighted above controls the voltage input to the controller Board. This two-way switch turns the kit's power on and off. You can use this to turn the robot off while keeping the battery pack plugged in. The switch does not affect the Pico W's power when a USB cable is plugged in.

## Motor Connectors

The controller board has four six-pin connectors labeled <b>Motor L</b>, <b>Motor R</b>, <b>Motor 3</b>, and <b>Motor 4</b> and two three-pin connectors labeled <b>Servo 1</b> and <b>Servo 2</b>. 

<figure markdown>
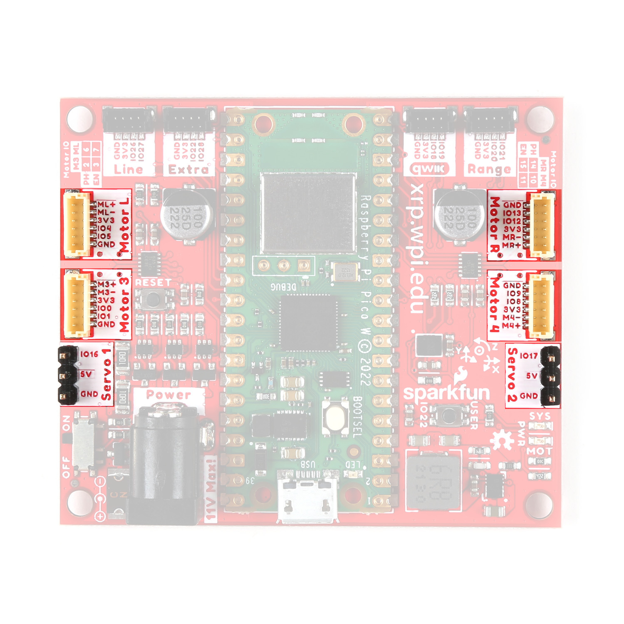
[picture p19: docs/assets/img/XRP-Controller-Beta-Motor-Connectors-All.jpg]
Photo highlighting the motor connectors.

</figure>

### DC Motor Connectors

The DC Motor connectors are where you'll plug in the left and right motors while assembling the kit. These connectors include the power connections for the motor as well as the encoders on the motors. The board routes these connections through the motor drivers to GPIO pins on the Pico W. You'll use these pins to monitor how many rotations the motor completes and use that data to determine how far the robot has traveled. Refer to the Pinout table at the end of this document for the specific GPIO pins each motor connects to on the Pico W. The controller board has two extra motor connectors for expansion projects using more than two motors.

### Servo Motor Connectors

The two three-pin connectors on either side of the board labeled Servo 1 and Servo 2 mate with servo motors. You'll use the Servo 2 connector to hook up the servo included in the XRP Kit - Beta. Servo 1 connector is an extra one for expansion projects. These connectors have power pins (<b>5V</b> and Ground) and a signal pin to control the motion of the servo motor. Servo motors use a communication method called pulse width modulation (PWM) that tells the motor to move and with some motors, where to move to. If you're interested in learning more about how servo motors work, you may want to check out SparkFun's [Servos Explained](https://www.sparkfun.com/servos) page for information and tutorials on how to use them.

## Expansion Connectors

The controller board has four four-pin connectors labeled (from left to right when looking at the labels upright) <b>Line</b>, <b>Extra</b>, <b>Qwiic</b>, and <b>Range</b>. Their labels indicate their use as well as which GPIO pins they connect to on the Pico W. These connectors provide an easy plug-in connection for the line follower and distance sensor as well as two extra connectors for expansion projects. These connectors are polarized meaning they only work when connected properly but they are keyed and there is only one way to plug a cable into them.

<figure markdown>
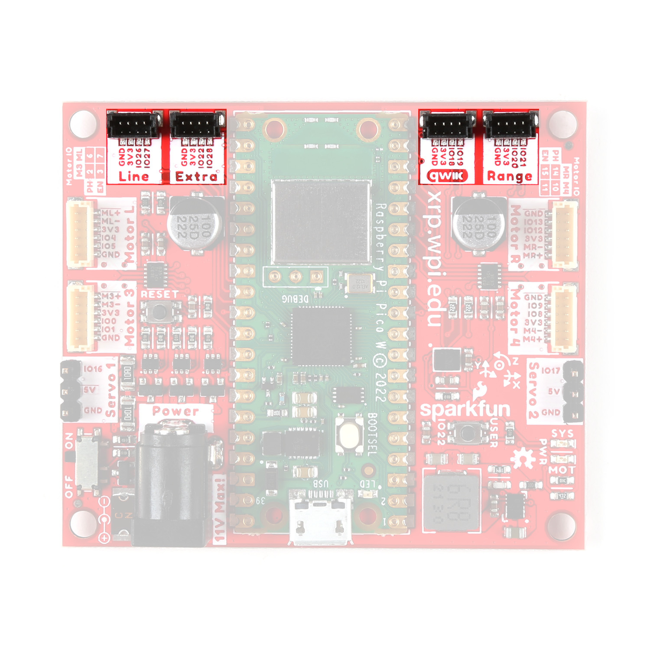
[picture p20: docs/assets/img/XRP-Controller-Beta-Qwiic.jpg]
Photo highlighting Qwiic and expansion connectors

</figure>

### Line Follower Connector

The Line connector is where you'll plug the cable for the line follower sensor into. This connects the sensor's two signal lines, Left and Right, to the Pico W's GPIO27 (Right) and GPIO26 (Left) pins. You'll use these pins to monitor whenever the sensor detects the robot has gone past the left or right threshold when performing line-following experiments.

### Range Sensor Connector

The Range connector is where you'll plug the cable for the ultrasonic range sensor into. It connects the distance sensor's Echo and Trigger lines to the Pico W's GPIO21 (Echo) and GPIO20 (Trig). You'll use these pins to receive distance data from the ultrasonic range sensor.

### Qwiic Connector

The Qwiic connector works with SparkFun's [Qwiic ecosystem](https://www.sparkfun.com/qwiic) of sensors that communicate over I<sup>2</sup>C. This is a two-wire communication protocol that works with a large variety of sensors and other electronics. With this, you can customize the XRP Kit - Beta to add things like environmental sensing, OLED screens, data logging, and more!

### Extra Connector

The Extra connector has pins for both power and ground as well as pins that connect to the Pico W's GPIO28 and GPIO22. Note, these pins are <i>shared</i> with other functionality on the XRP Controller - Beta. GPIO28 is shared with the VIN Measure pin which lets you measure the voltage level on VIN so you can monitor the remaining battery charge. GPIO22 is shared with the User Button. Both pins' primary functions can be disabled with the solder jumpers, refer to the Solder Jumpers section below for more information.

## Buttons

The XRP Controller - Beta has three push buttons labeled <b>USER</b>, <b>RESET</b>, and <b>BOOTSEL</b> (on the Pico W). The USER button connects to GPIO22 on the Pico W which allows it to be programmed for various purposes. The RESET button does just what its name suggests and resets the entire board when pressed. This can help to reboot the robot or to restart a sequence you want the Robotics Kit to perform. Holding the BOOTSEL button either when plugging in a USB cable or when pressing the RESET button sets the Pico W to behave as a mass storage device when connected to a computer for uploading firmware. 

<figure markdown>
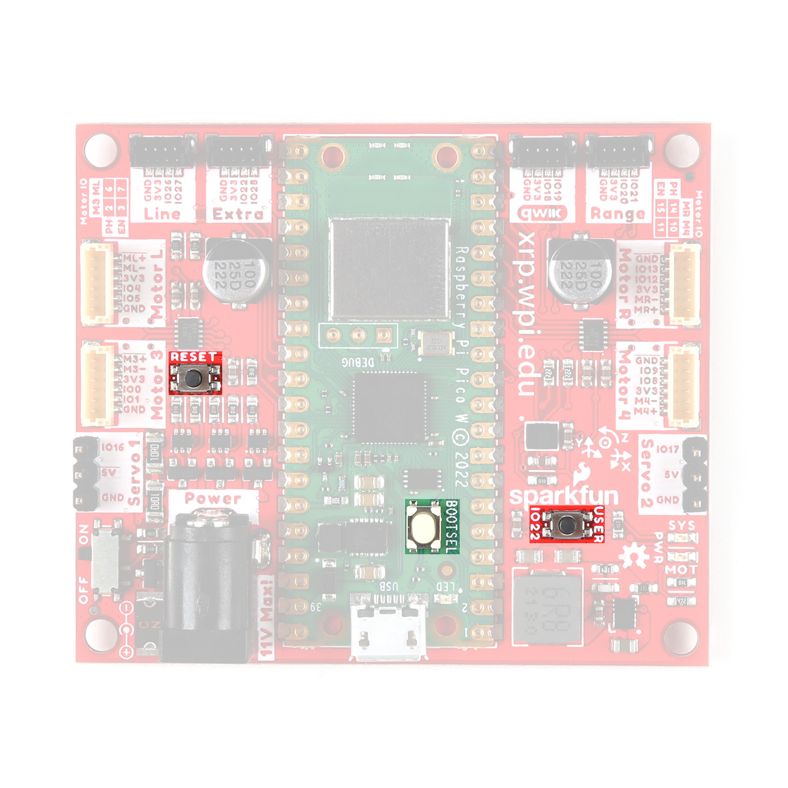
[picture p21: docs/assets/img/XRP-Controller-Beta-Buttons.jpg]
Photo highlighting buttons.

</figure>

## LEDs

There are three LEDs on the XRP Controller - Beta labeled <b>MOT</b>, <b>SYS</b>, and <b>LED</b>. 

<figure markdown>
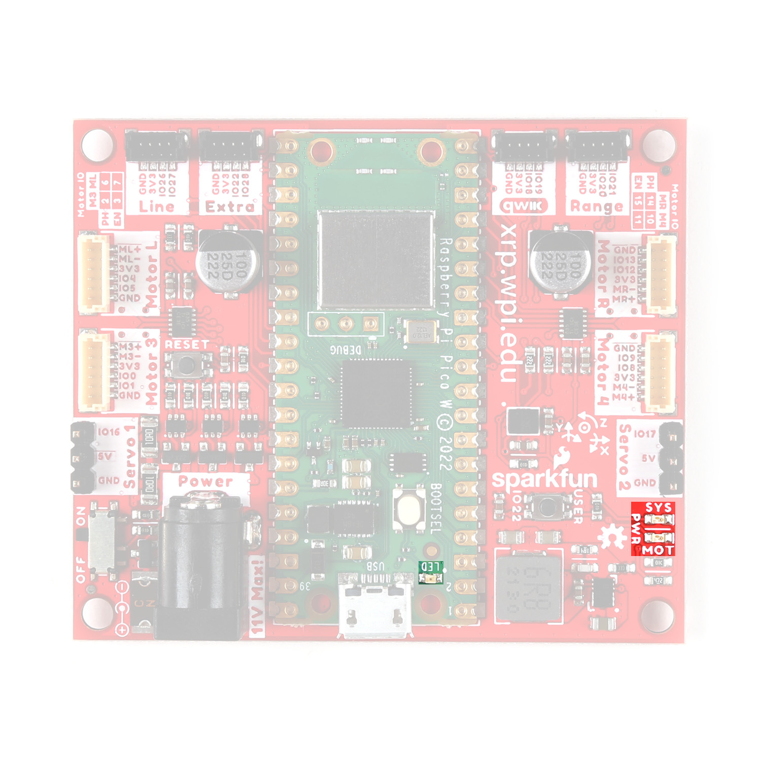
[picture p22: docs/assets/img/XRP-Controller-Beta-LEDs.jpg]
Photo highlighting LEDs

</figure>

These LEDs provide a visual indication to the user. The LEDs labeled <b>MOT</b> and <b>SYS</b> turn on when their respective power rails are powered. The <b>MOT</b> LED turns on when the motors have power available. The <b>SYS</b> LED turns on when the <b>3.3V</b>/System circuit is powered. This circuit powers the Pico W, sensors, and the expansion connectos. The LED on the Pico W labeled <b>LED</b> is a user-programmable status LED you can program for whatever behavior you prefer. For example, you can have it turn on when the distance sensor reports a certain distance.  

## Solder Jumpers

!!! warning Advanced Users Only

    These solder jumpers can change the behavior of the board in a lasting way. Using these requires extra tools not included in the XRP
     Kit - Beta along with knowledge of how to use and interact with solder jumpers. We recommend that only advanced users adjust and change the solder jumpers. If you'd like to learn more about how to use solder jumpers, check out SparkFun's [How to Work with Jumper Pads and PCB Traces](https://learn.sparkfun.com/tutorials/how-to-work-with-jumper-pads-and-pcb-traces) tutorial.

Lastly, the XRP Controller - Beta has nine solder jumpers. A solder jumper provides a customization option for advanced users to control the behavior of the pins and components they connect to. The solder jumpers on this board are labeled (from top-to-bottom when looking at the photo below): <b>VIN_MEAS</b>, <b>MOT_MODE_R/4</b>, <b>MOT_MODE_L/3</b>, <b>USER_BTN</b>, <b>I2C</b>, <b>IMU_ADR</b>, <b>SYS</b>, <b>MOT</b>, and <b>VUSB</b>. 

<figure markdown>
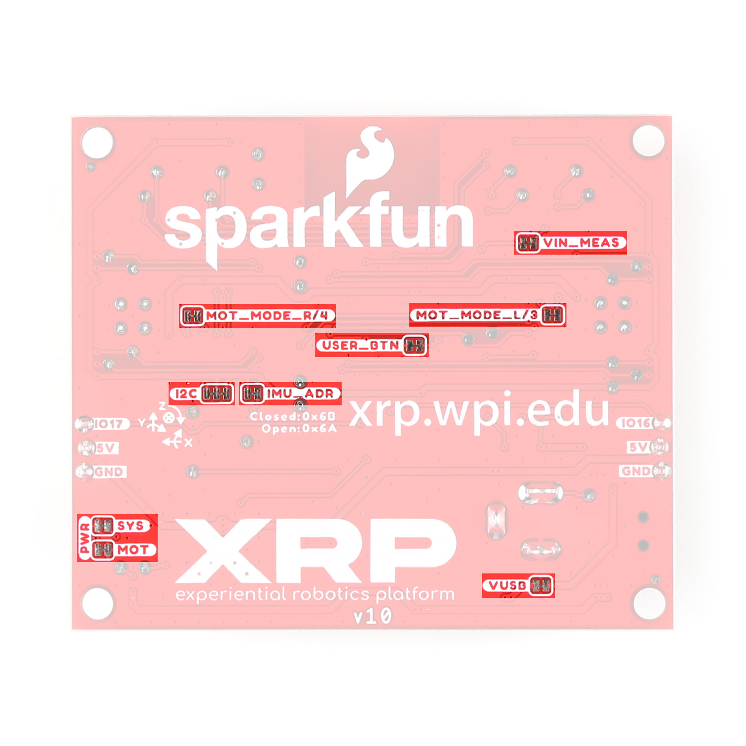
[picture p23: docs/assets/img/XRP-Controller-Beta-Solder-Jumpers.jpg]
Photo highlighting solder jumpers.

</figure>

<table>
    <tr>
        <th>Label</th>
        <th>Default State</th>
        <th>Function</th>
        <th>Notes</th>
    </tr>
    <tr>
        <td>VIN_MEAS</td>
        <td>CLOSED</td>
        <td>Completes the VIN circuit.</td>
        <td>Open to disrupt the VIN circuit to measure voltage on VIN with a multimeter.</td>
    </tr>
    <tr>
        <td>MOT_MODE_R/4</td>
        <td>CLOSED</td>
        <td>Pulls the Right DRV8835's MODE pin to <b>3.3V</b>.</td>
        <td>This sets the DRV8835 to run in PH/EN mode by default. Open to switch the DRV8835 to operate in IN/IN mode.</td>
    </tr>
    <tr>
        <td>MOT_MODE_L/3</td>
        <td>CLOSED</td>
        <td>Pulls the Left DRV8835's MODE pin to <b>3.3V</b>.</td>
        <td>This sets the DRV8835 to run in PH/EN mode by default. Open to switch the DRV8835 to operate in IN/IN mode.</td>
    </tr>
    <tr>
        <td>USER_BTN</td>
        <td>CLOSED</td>
        <td>Completes the User Button circuit to tie it to GPIO22.</td>
        <td>Open to disconnect the button from GPIO22.</td>
    </tr>
    <tr>
        <td>I2C</td>
        <td>CLOSED</td>
        <td>Pulls the SDA/SCL lines to <b>3.3V</b> through two <b>2.2k&ohm;</b>.</td>
        <td>Open completely to disable the pull up resistors on the I<sup>2</sup>C bus.</td>
    </tr>
    <tr>
        <td>IMU_ADR</td>
        <td>CLOSED</td>
        <td>Sets the IMU's I<sup>2</sup>C address to <b>0x6B</b>.</td>
        <td>Open to switch the I<sup>2</sup>C address to <b>0x6A</b>.</td>
    </tr>
    <tr>
        <td>SYS</td>
        <td>CLOSED</td>
        <td>Completes the SYS Power LED circuit.</td>
        <td>Open to disable the SYS Power LED.</td>
    </tr>
    <tr>
        <td>MOT</td>
        <td>CLOSED</td>
        <td>Completes the MOT Power LED circuit.</td>
        <td>Open to disable the MOT Power LED.</td>
    </tr>
    <tr>
        <td>VUSB</td>
        <td>CLOSED</td>
        <td>Completes the V_USB circuit to provide <b>5V</b> and <b>3.3V</b> to the board from USB.</td>
        <td>Open to prevent motors and servos from being powered by USB.</td>
    </tr>
</table>

## Pinout Reference Table

The table below offers a quick reference for the complete pinout on the XRP Controller - Beta and which pins they connect to on the Pico W. 

<table>
    <tr>
        <th>Pico W GPIO Pin</th>
        <th>Connector Label</th>
        <th>Pin Function</th>
    </tr>
    <tr>
        <td>GPIO0</td>
        <td>Motor 3</td>
        <td>Motor 3 Encoder A</td>
    </tr>
    <tr>
        <td>GPIO1</td>
        <td>Motor 3</td>
        <td>Motor 3 Encoder B</td>
    </tr>
    <tr>
        <td>GPIO2</td>
        <td>Motor 3</td>
        <td>Motor 3 Phase Pin</td>
    </tr>
    <tr>
        <td>GPIO3</td>
        <td>Motor 3</td>
        <td>Motor 3 Enable Pin</td>
    </tr>
    <tr>
        <td>GPIO4</td>
        <td>Motor L</td>
        <td>Left Motor Encoder A</td>
    </tr>
    <tr>
        <td>GPIO5</td>
        <td>Motor L</td>
        <td>Left Motor Encoder B</td>
    </tr>
    <tr>
        <td>GPIO6</td>
        <td>Motor L</td>
        <td>Left Motor Phase Pin</td>
    </tr>
    <tr>
        <td>GPIO7</td>
        <td>Motor L</td>
        <td>Left Motor Enable Pin</td>
    </tr>
    <tr>
        <td>GPIO8</td>
        <td>Motor 4</td>
        <td>Motor 4 Encoder A</td>
    </tr>
    <tr>
        <td>GPIO9</td>
        <td>Motor 4</td>
        <td>Motor 4 Encoder B</td>
    </tr>
    <tr>
        <td>GPIO10</td>
        <td>Motor 4</td>
        <td>Motor 4 Phase Pin</td>
    </tr>
    <tr>
        <td>GPIO11</td>
        <td>Motor 4</td>
        <td>Motor 4 Enable Pin</td>
    </tr>
    <tr>
        <td>GPIO12</td>
        <td>Motor R</td>
        <td>Right Motor Encoder A</td>
    </tr>
    <tr>
        <td>GPIO13</td>
        <td>Motor R</td>
        <td>Right Motor Encoder B</td>
    </tr>
    <tr>
        <td>GPIO14</td>
        <td>Motor R</td>
        <td>Right Motor Phase Pin</td>
    </tr>
    <tr>
        <td>GPIO15</td>
        <td>Motor R</td>
        <td>Right Motor Enable Pin</td>
    </tr>
    <tr>
        <td>GPIO16</td>
        <td>Servo 1</td>
        <td>Servo 1 Signal Pin</td>
    </tr>
    <tr>
        <td>GPIO17</td>
        <td>Servo 2</td>
        <td>Servo 2 Signal Pin</td>
    </tr>
    <tr>
        <td>GPIO18</td>
        <td>Qwiic</td>
        <td>Qwiic Data Signal for the IMU & Qwiic Connector</td>
    </tr>
    <tr>
        <td>GPIO19</td>
        <td>Qwiic</td>
        <td>Qwiic Clock Signal for the IMU & Qwiic Connector</td>
    </tr>
    <tr>
        <td>GPIO20</td>
        <td>Range</td>
        <td>Range Trigger Pin</td>
    </tr>
    <tr>
        <td>GPIO21</td>
        <td>Range</td>
        <td>Range Echo Pin</td>
    </tr>
    <tr>
        <td>GPIO22</td>
        <td>Extra</td>
        <td>User Button/Extra</td>
    </tr>
    <tr>
        <td>GPIO26</td>
        <td>Line</td>
        <td>Line Follower Left Signal</td>
    </tr>
    <tr>
        <td>GPIO27</td>
        <td>Line</td>
        <td>Line Follower Right Signal</td>
    </tr>
    <tr>
        <td>GPIO28</td>
        <td>Extra</td>
        <td>VIN_Meas/Extra</td>
    </tr>
</table>

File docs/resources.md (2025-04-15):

For more information about both versions of the XRP Controller covered in this document, take a look at the following resources:

**XRP Controller Resources**

 * [Schematic (PDF)](./assets/hardware_files/SparkFun-XRP-Controller-Schematic.pdf)
 * [KiCad Files (ZIP)](./assets/hardware_files/SparkFun_XRP_Controller-KiCad.zip)
 * [Board Dimensions](./assets/hardware_files/SparkFun-XRP-Controller-Dimensions.jpg)
 * [RP2350 Datasheet](./assets/component_documentation/rp2350-datasheet.pdf)
 * [DRV8411 Motor Driver Datasheet](./assets/component_documentation/drv8411a.pdf)
 * [LSM6DSO 6 DoF IMU Datasheet](./assets/component_documentation/LSM6DSO.pdf)

**XRP Controller - Beta Resources**

* [Schematic (PDF)](./assets/hardware_files/XRP_Controller_Beta.pdf)
* [Eagle Files (ZIP)](./assets/hardware_files/XRP_Controller_Beta.zip)
* [Raspberry Pico W Datasheet](./assets/component_documentation/pico-w-datasheet.pdf)
* [DRV8835 Motor Driver Datasheet](./assets/component_documentation/drv8835.pdf)
* [LSM6DSO 6 DoF IMU Datasheet](./assets/component_documentation/LSM6DSO.pdf)

**General XRP Resources**

* [XRP Robotis Platform Home Page](https://experientialrobotics.org/)
* [GitHub Hardware Repository](https://github.com/sparkfun/SparkFun_XRP_Controller)
* [XRP Chassis 3D Printing Files](https://www.printables.com/model/1216372-xrp-robot-kit)
* [XRP Chassis 3D Printing Files - Beta Version](https://www.printables.com/model/576581-xrp-robot-part-of-the-experiential-consortia)

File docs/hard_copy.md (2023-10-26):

---
icon: material/book-open-variant
---

Need to download or print our hookup guide?

* [Print :fontawesome-solid-print:](../single_page) (Single-Page View)
    * To save as a `*.pdf` file, select the **Printer** or **Destination** labeled ++"Save as PDF"++. *(Instructions will vary based on the browser)*

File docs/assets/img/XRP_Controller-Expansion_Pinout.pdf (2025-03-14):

Color Code | XRP Usage | Header Pin Pin Header | XRP Usage | XRP Usage | Header Pin Pin Header | XRP Usage
Ground | MotorL/3 Current Limit | ML/3 VREF | 61 21 | GPIO16 | Free | Radio Module | Free | GPIO15 | 20 60 | MR/4 Fault | MotorR/4 Driver Fault
Power | MotorL/3 Driver Fault | ML/3 Fault | 62 22 | GPIO17 | Free | | Free | GPIO14 | 19 59 | MR/4 VREF | MotorR/4 Current Limit
Control Signal | GND GND | | 63 23 | GND GND | | | GND GND | | 18 58 | GND GND
Status Signal | Encoder LA | GPIO30 | 64 24 | GPIO18 | Free | | Free | GPIO13 | 17 57 | GPIO33 | Motor R IN2
RP2350 GPIO | Encoder LB | GPIO31 | 65 25 | GPIO19 | Free | | Free | GPIO12 | 16 56 | GPIO32 | Motor R IN1
Radio GPIO | Motor L IN1 | GPIO34 | 66 26 | GPIO20 | Motor 3 IN1 | | Motor 4 IN2 | GPIO11 | 15 55 | GPIO25 | Encoder RB
LED | Motor L IN2 | GPIO35 | 67 27 | GPIO21 | Motor 3 IN2 | | Motor 4 IN1 | GPIO10 | 14 54 | GPIO24 | Encoder RA
Button/Switch | GND GND | | 68 28 | GND GND | | | GND GND | | 13 53 | GND GND
Motor | Encoder 3B | GPIO23 | 69 29 | GPIO22 | Encoder 3A | | Servo 2 | GPIO09 | 12 52 | WL_IO2 | Free
Servo | Power Good | PG | 70 30 | RUN | Reset Button | | Servo 4 | GPIO08 | 11 51 | WL_IO1 | Free
Sensor | Motor L Current | GPIO40 | 71 31 | GPIO44 | Line L | | Servo 3 | GPIO07 | 10 50 | GPIO43 | Motor R Current
I2C (Qwiic) | Motor 3 Current | GPIO41 | 72 32 | GPIO45 | Line R | | Servo 1 | GPIO06 | 9 49 | GPIO42 | Motor 4 Current
Free for User | GND GND | | 73 33 | GND GND | | | GND GND | | 8 48 | GND GND
Not Connected | WS2812 RGB LED | RGB_OUT | 74 34 | GPIO46 | VIN Measure | | Qwiic0 SCL | GPIO05 | 7 47 | GPIO39 | Qwiic1 SCL (IMU)
| Servo Power 5V After Power Switch VIN | | 75 35 76 36 | VREF Analog Reference 3V3 System Power | | | Qwiic0 SDA | GPIO04 | 6 46 | GPIO38 | Qwiic1 SDA (IMU)
| | | | | | | Encoder 4B | GPIO03 | 5 45 | IMU INT1 | IMU Interrupt 1
| Main Power Switch | VIN_EN | 77 37 | 3V3_EN | 3V3 Regulator Enable | | Encoder 4A | GPIO02 | 4 44 | IMU INT2 | IMU Interrupt 2
| GND GND | | 78 38 | GND GND | | | GND GND | | 3 43 | GND GND
| Before Power Switch VRAW Battery Power VBATT | | 79 39 80 40 | VSYS Before 3.3V Regulator VBUS USB Power | | USB-C | Distance Echo Distance Trigger | GPIO01 GPIO00 | 2 42 1 41 | BOOTSEL | Boot Button
| | | | | | | | | | GPIO36 | User Button

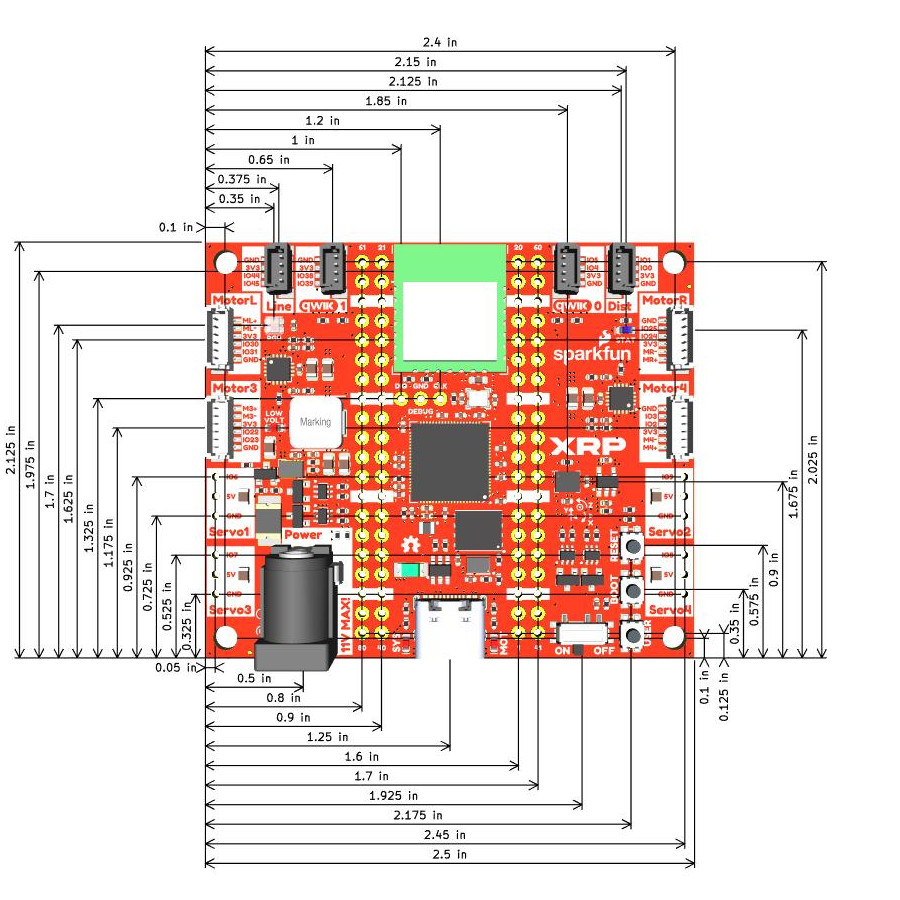
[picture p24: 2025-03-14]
docs/assets/hardware_files/SparkFun-XRP-Controller-Dimensions.jpg

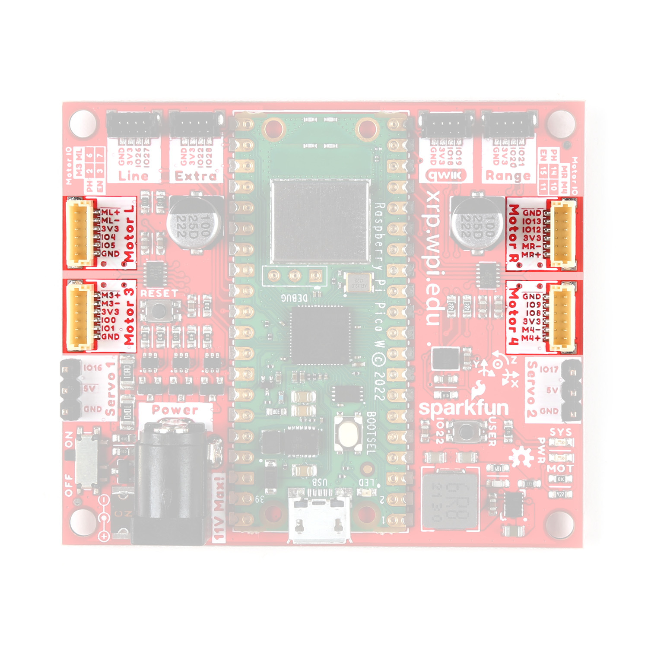
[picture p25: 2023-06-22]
docs/assets/img/XRP-Controller-Beta-DC-Motors.jpg

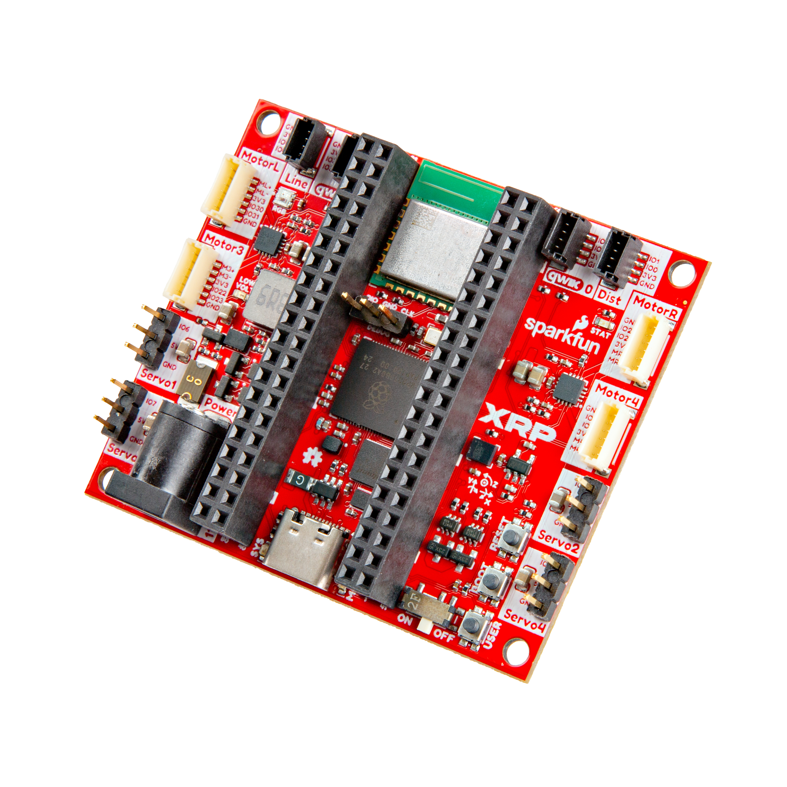
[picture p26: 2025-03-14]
docs/assets/img/XRP-Controller-Feature.jpg

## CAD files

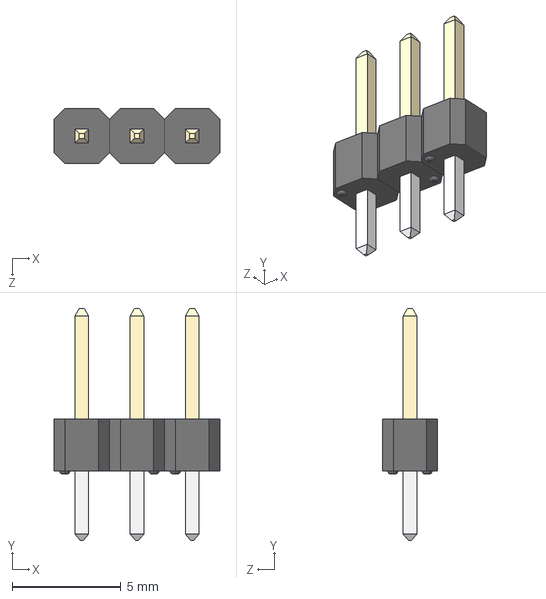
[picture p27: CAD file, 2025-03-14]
Hardware/SparkFun_XRP_Controller_3D_Models/header_male_1x3.STEP
7.62 x 10.7 x 2.54 mm
P(B,C)C01SAAN x 3

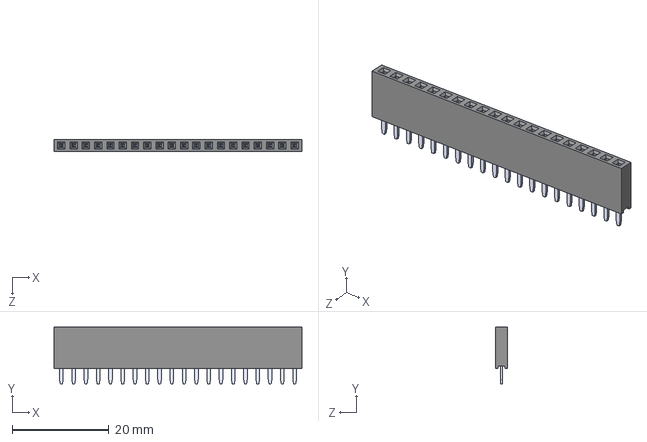
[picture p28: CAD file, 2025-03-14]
Hardware/SparkFun_XRP_Controller_3D_Models/header_female_1x20.STEP
51.3 x 11.7 x 2.54 mm

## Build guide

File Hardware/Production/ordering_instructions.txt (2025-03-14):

Ordering Instructions:
Panel dimensions: 141.20 x 176.62 mm.
Controlled Impedance: JLC06161H-3313
Material: TG155
Solder Mask: Red
Silkscreen Color: White
Layers: 6
Finish: ENIG
Thickness: 1.6mm
Inner Copper Weight: 0.5oz
Outer Copper Weight: 1oz
Minimum track width: 0.13mm (5.00mil)
Minimum via drill: 0.30mm (11.81mil)
No Clean Process

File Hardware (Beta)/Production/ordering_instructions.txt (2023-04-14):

panel size, 142x177mm
PCB thickness, 1.6mm
number of layers, 2
soldermask color, Red
silkscreen color, White
oz copper, 1oz
finish, HASL lead free
stencils, top
pcs per panel, 6
min trace width, 0.2540mm / 0.0100in
min drill size, 0.3048mm / 0.0120in

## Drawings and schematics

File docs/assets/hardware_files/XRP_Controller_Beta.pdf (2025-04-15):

J31 1 | 2 2 | 3 3 | 4 4 | 5 5 | 6 6
J41 1 | 2 2 | 3 3 | 4 4 | 5 5 | 6 6

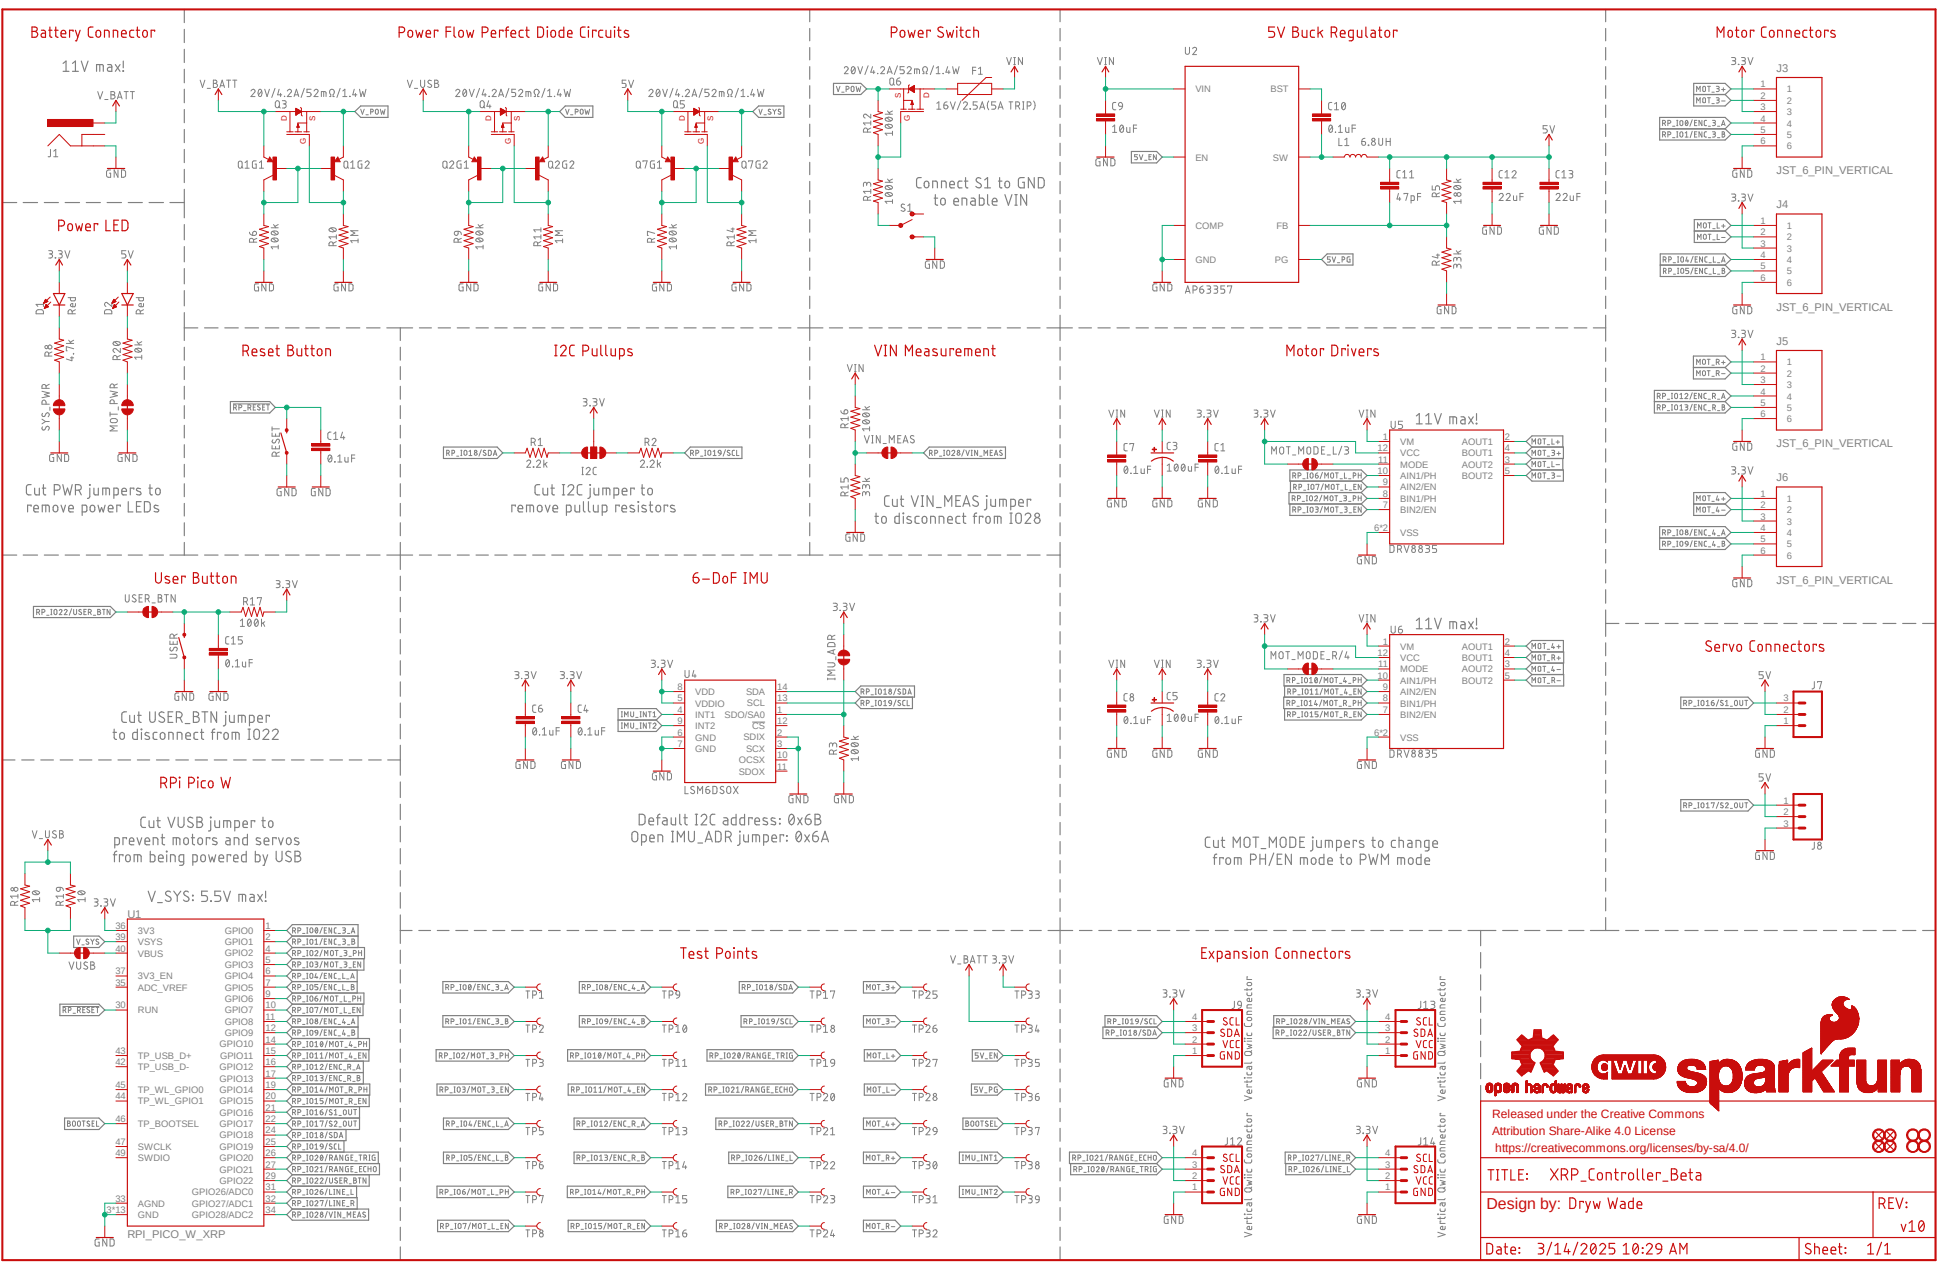
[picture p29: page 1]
JST_6_PIN_VERTICAL; RPI_PICO_W_XRP; INT2 9; SDOX 11 OCSX 10 SCL 13 SCX 3 SDA 14 SDO/SA0 1 SDIX 2 VDD 8 VDDIO 5; AIN1/PH 10 AIN2/EN 9; AOUT1 2 AOUT2 3 BIN1/PH 8 BIN2/EN 7; BOUT1 4 BOUT2 5 MODE 11 VCC 12 VM 1 VSS 6*2 AIN1/PH 10 AIN2/EN 9; BOUT1 4 BOUT2 5 MODE 11 VCC 12 VM 1 VSS 6*2 1234; VIN; COMP GND; BST; RUN 30; 3V3_EN 37 AGND 33 TP_USB_D+ 43 TP_USB_D- 42 GND 3*13; VSYS 39; GPIO0 1 ADC_VREF 35 SWDIO 49 SWCLK 47 VBUS 40 TP_WL_GPIO0 45 TP_WL_GPIO1 44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

INT1 4
CS 12 GND 6 GND 7

https://creativecommons.org/licenses/by-sa/4.0/

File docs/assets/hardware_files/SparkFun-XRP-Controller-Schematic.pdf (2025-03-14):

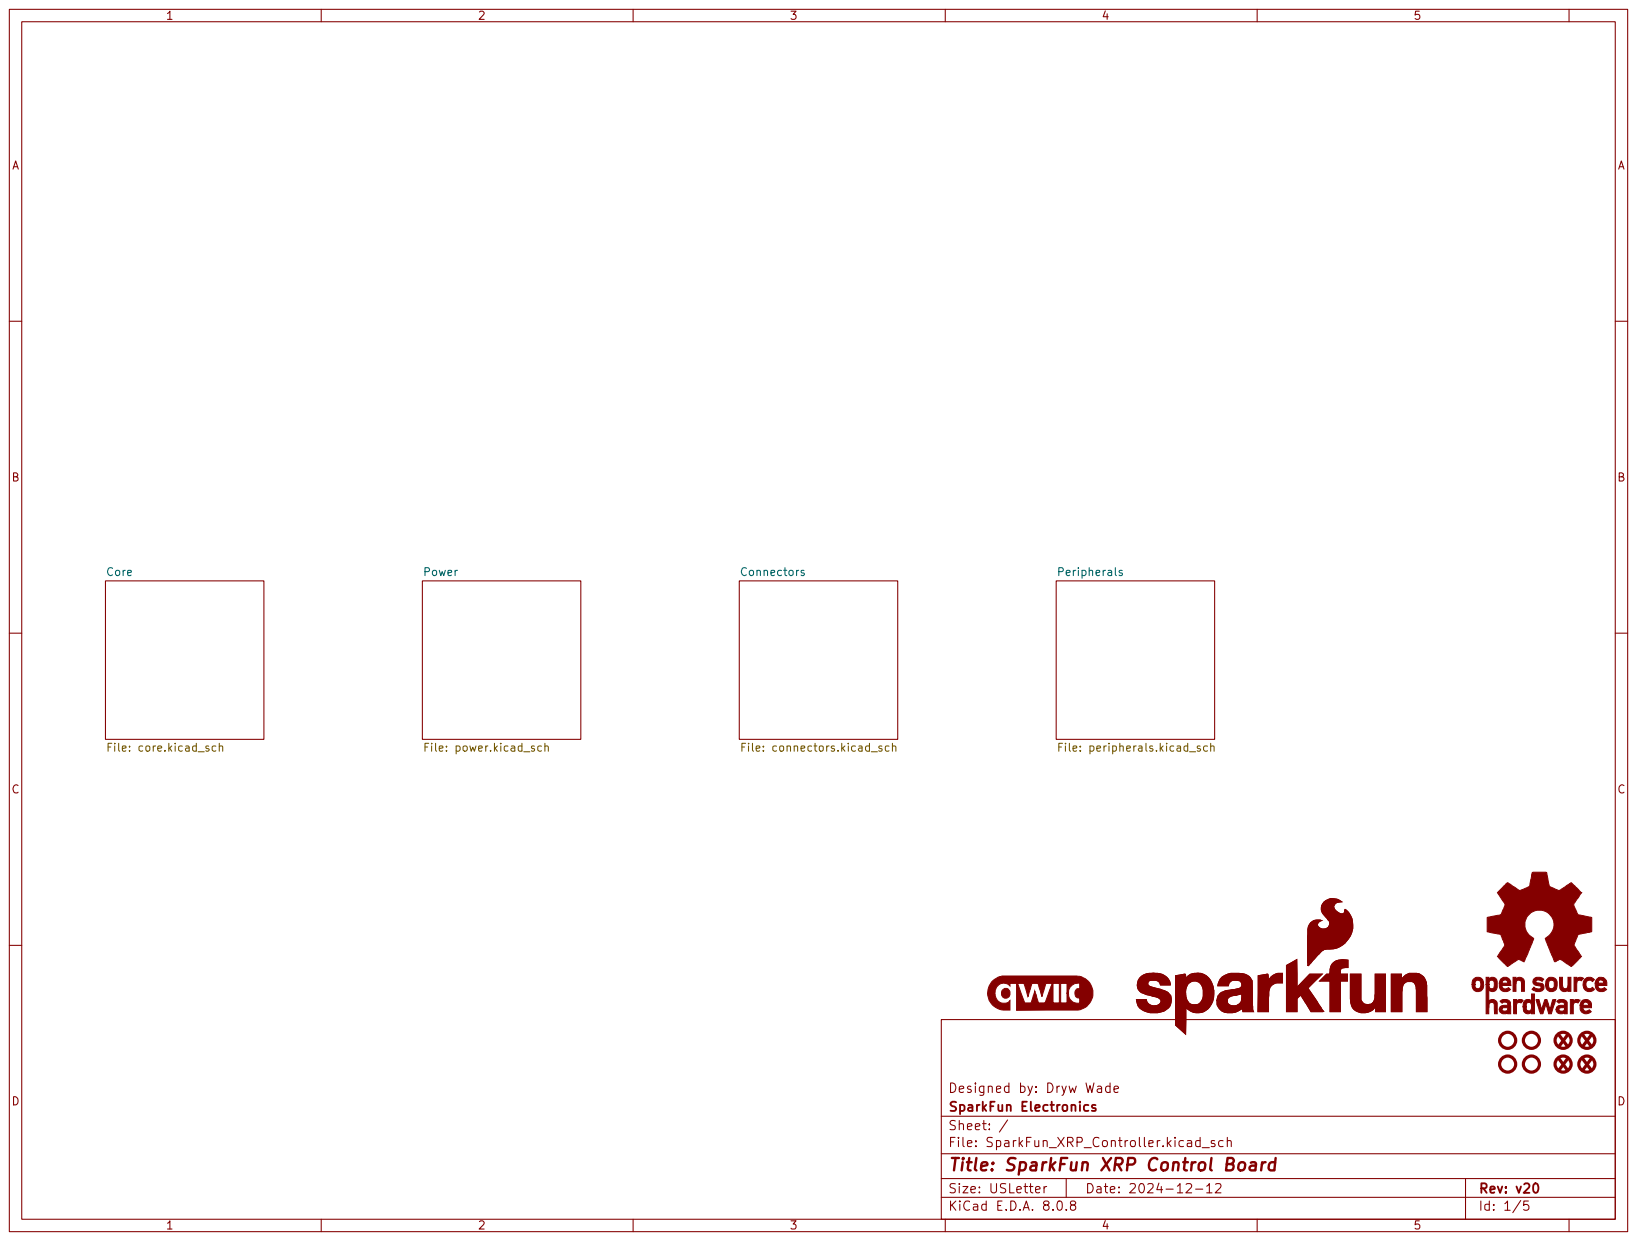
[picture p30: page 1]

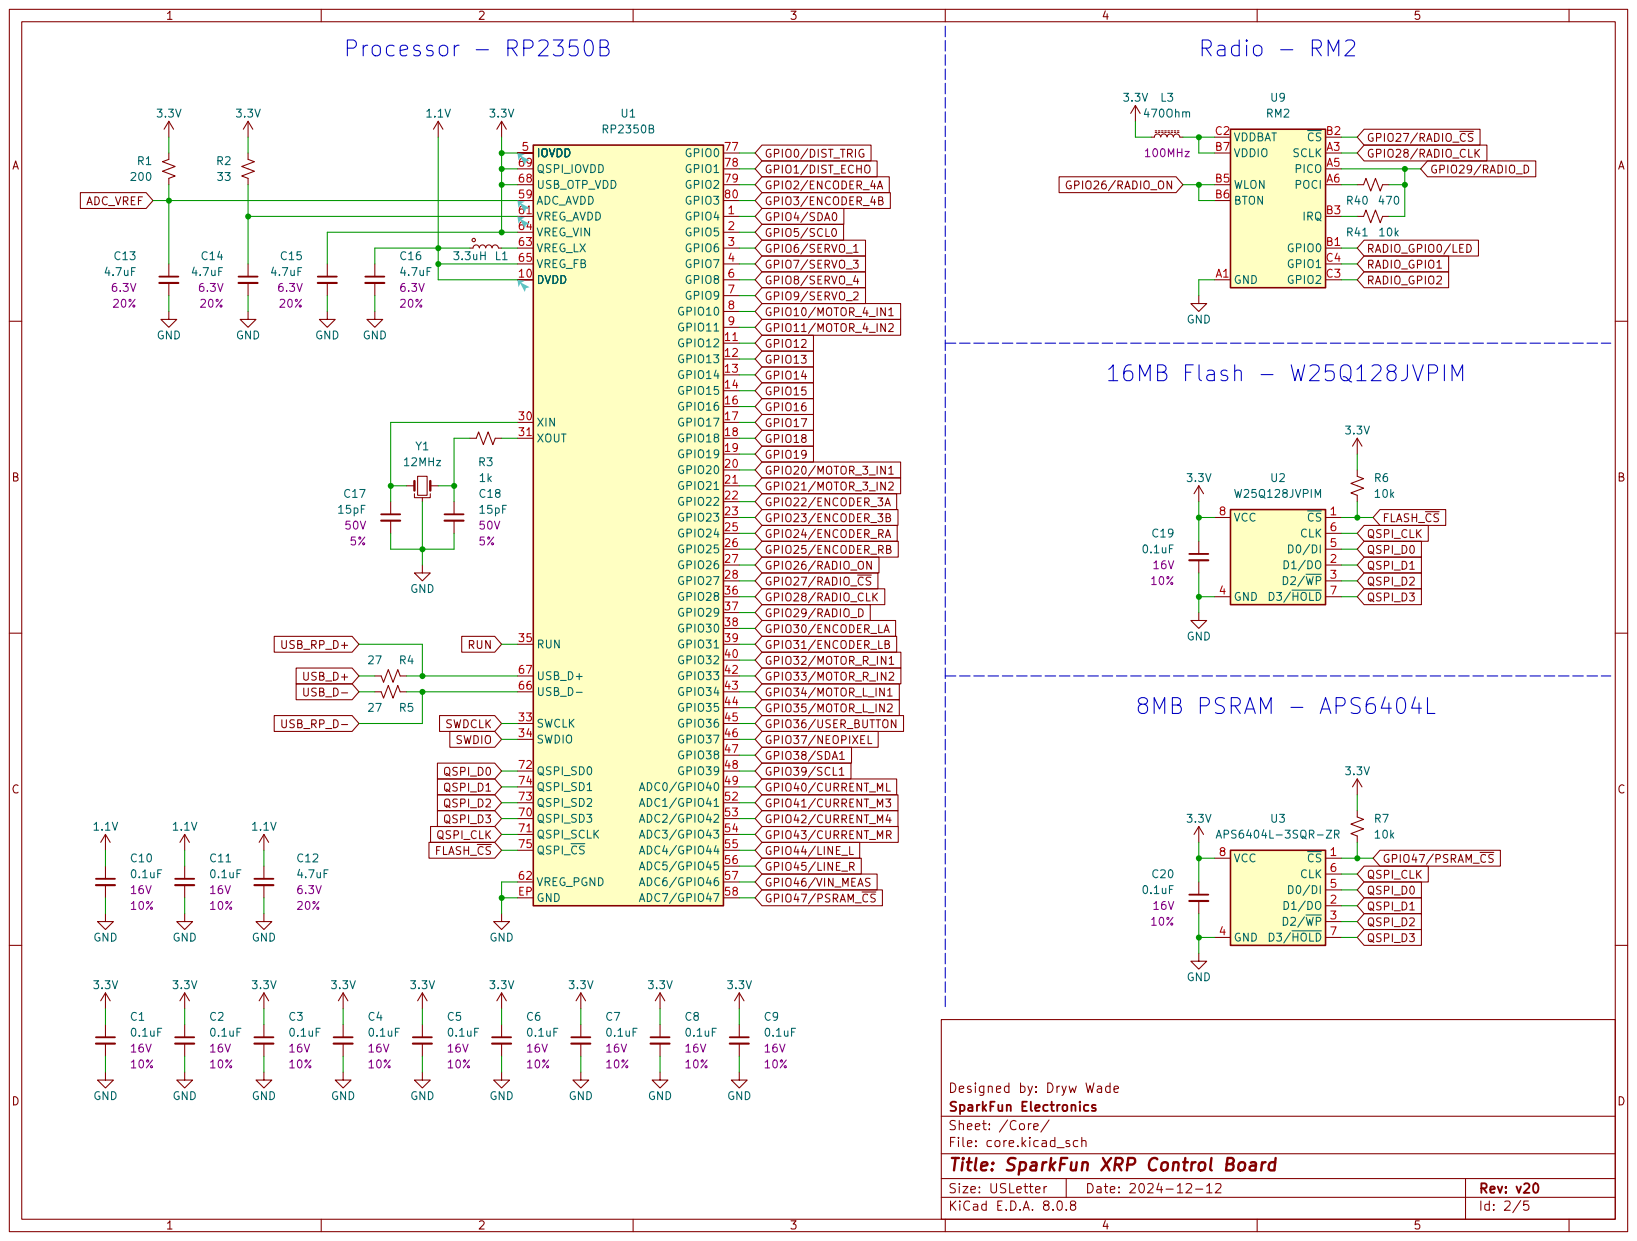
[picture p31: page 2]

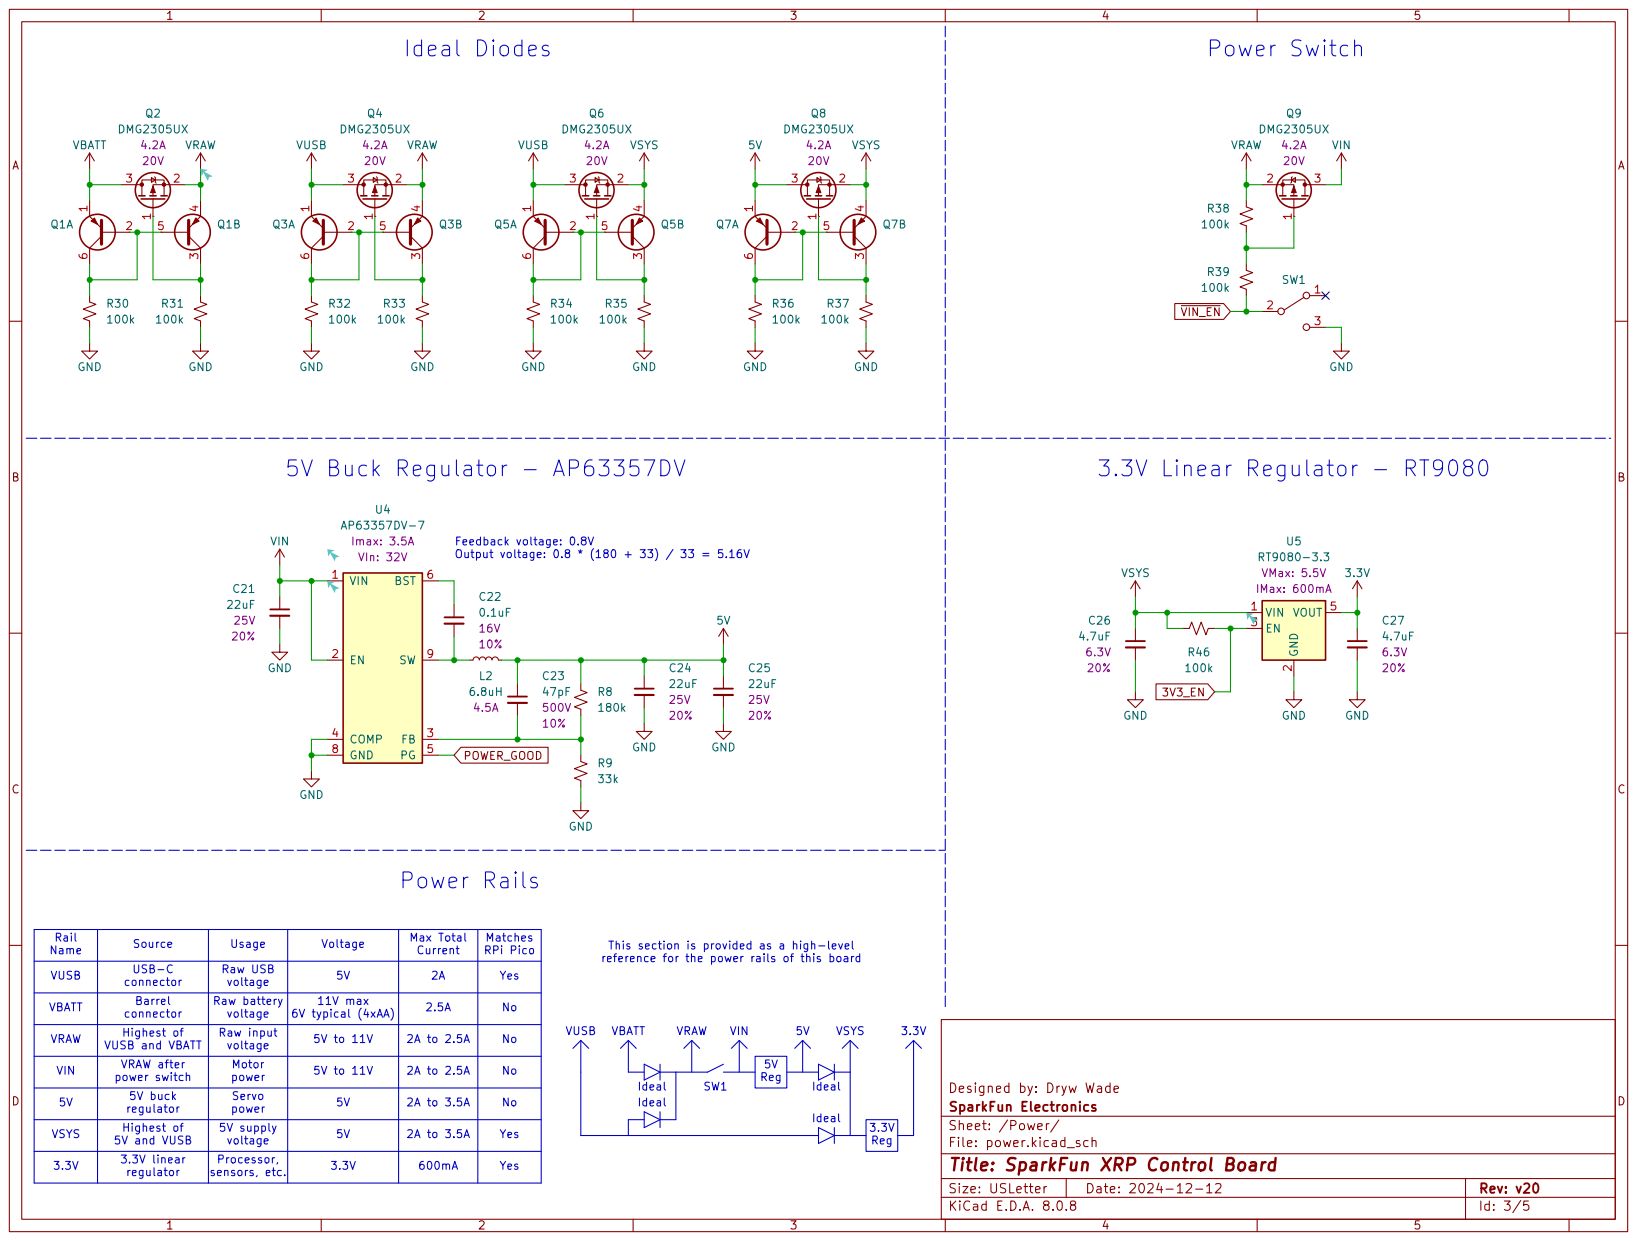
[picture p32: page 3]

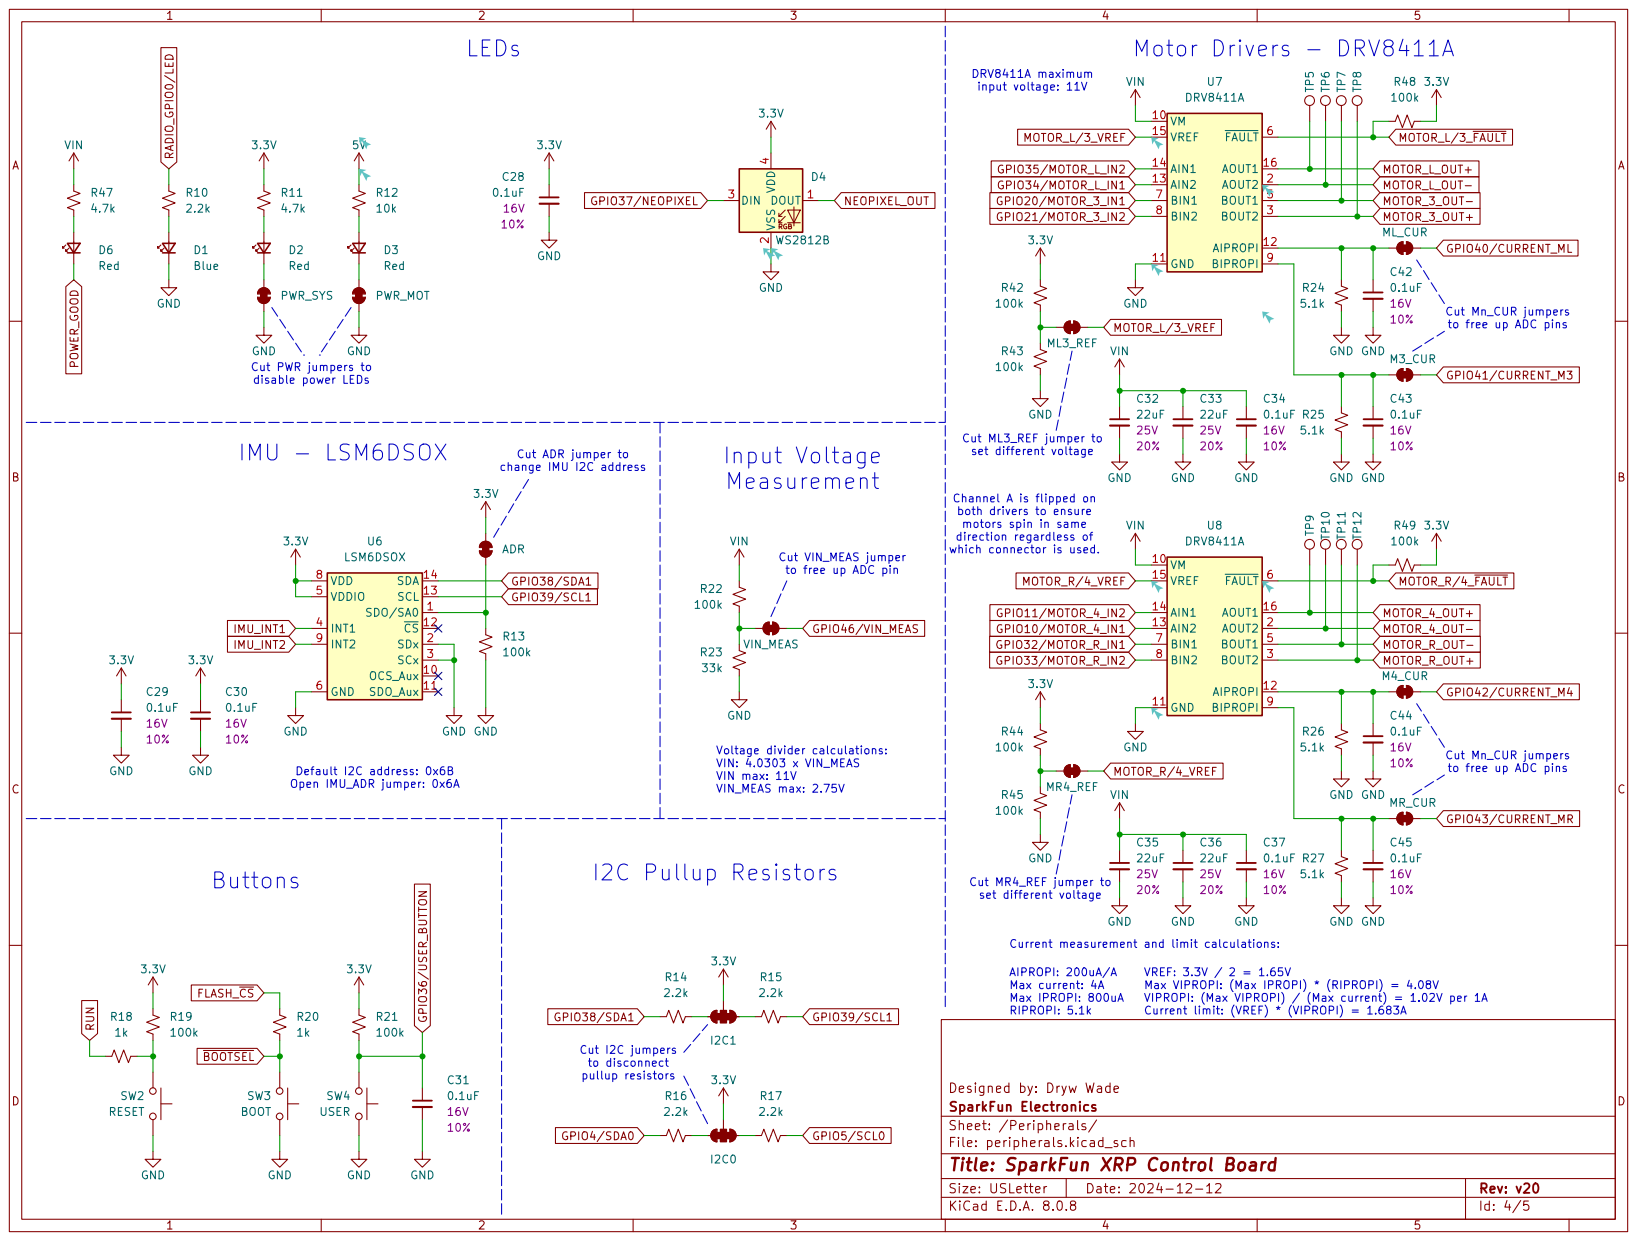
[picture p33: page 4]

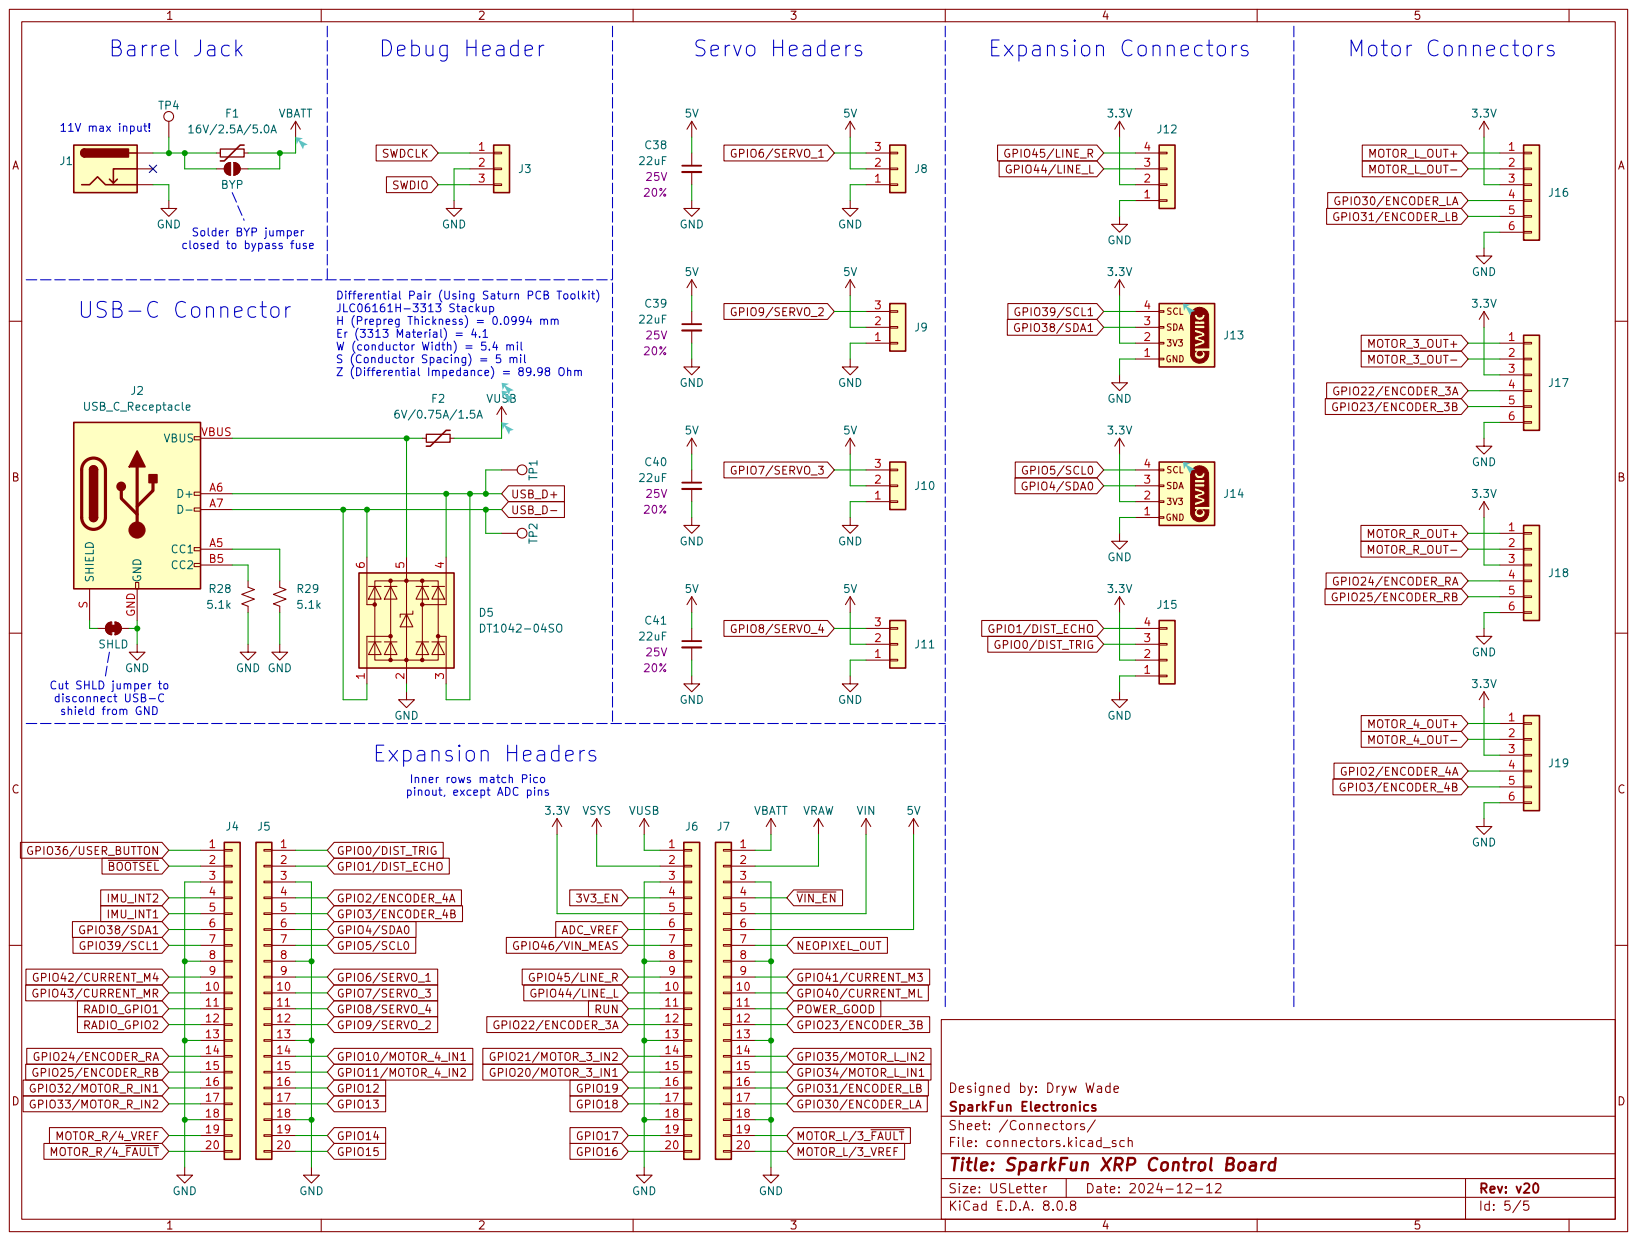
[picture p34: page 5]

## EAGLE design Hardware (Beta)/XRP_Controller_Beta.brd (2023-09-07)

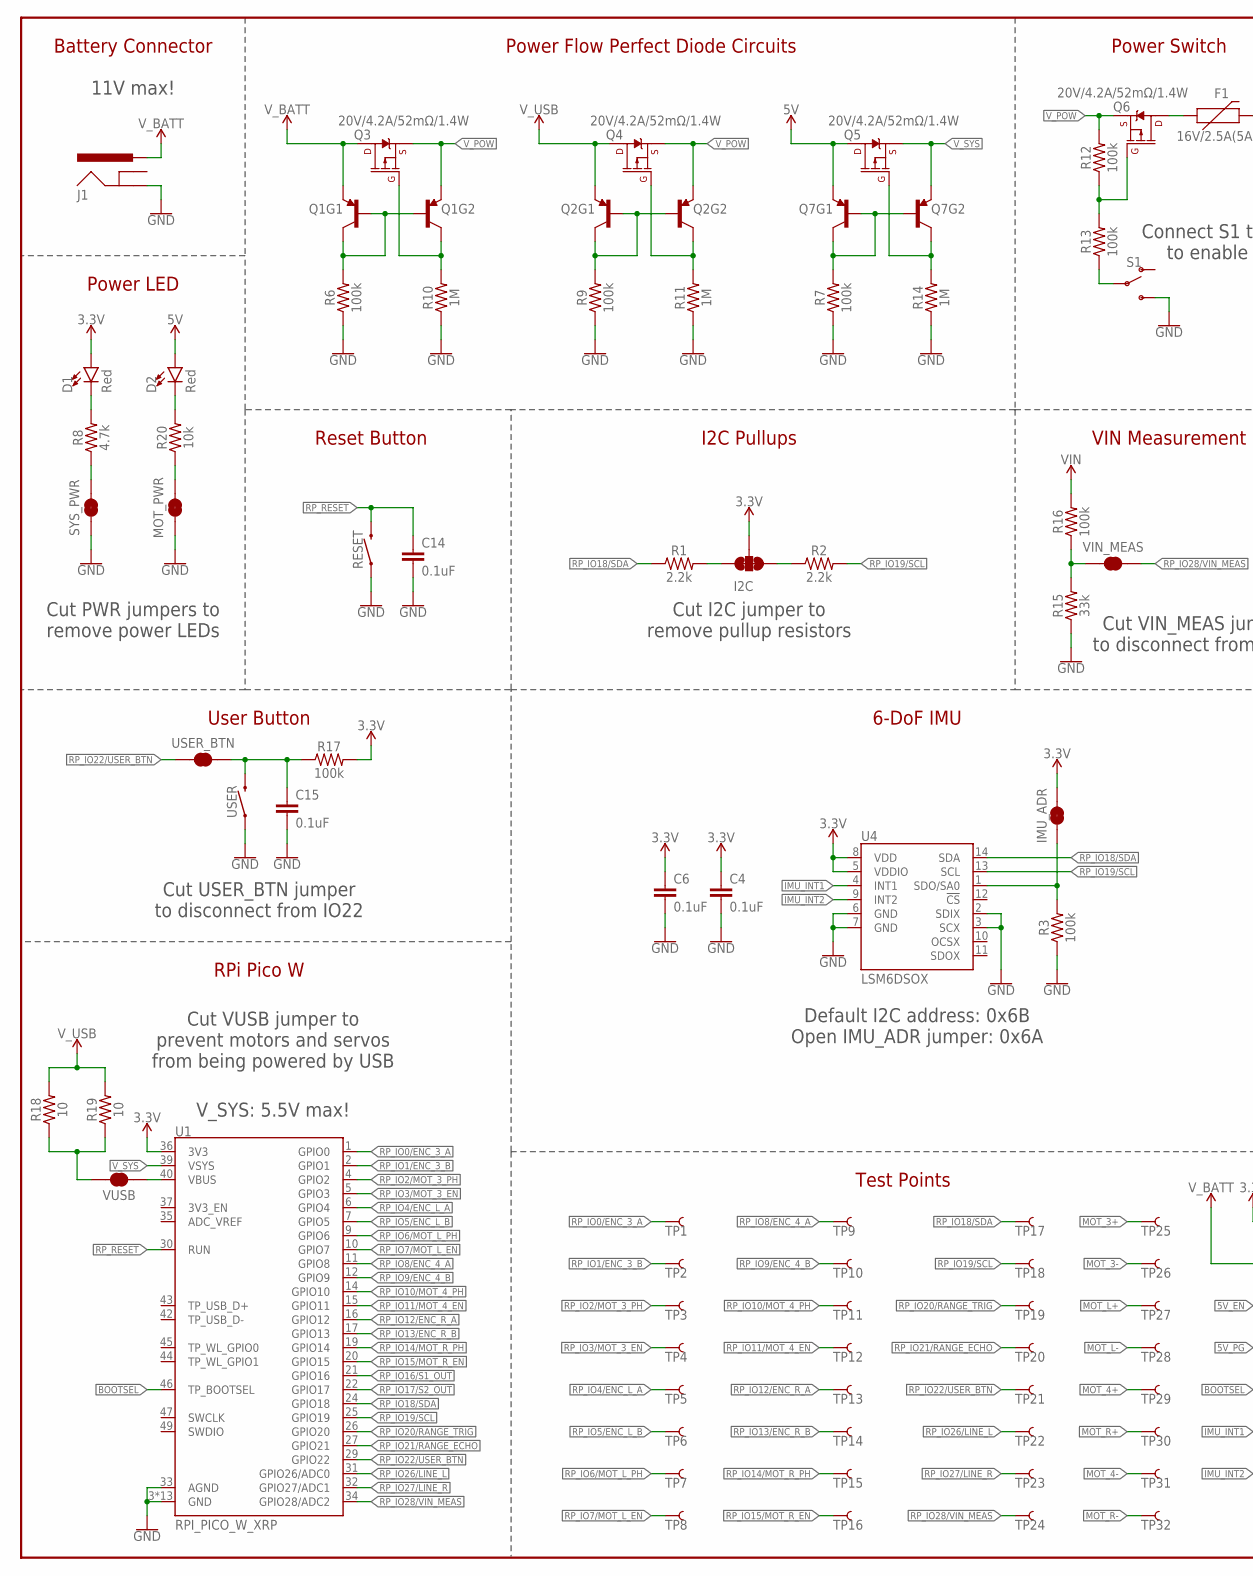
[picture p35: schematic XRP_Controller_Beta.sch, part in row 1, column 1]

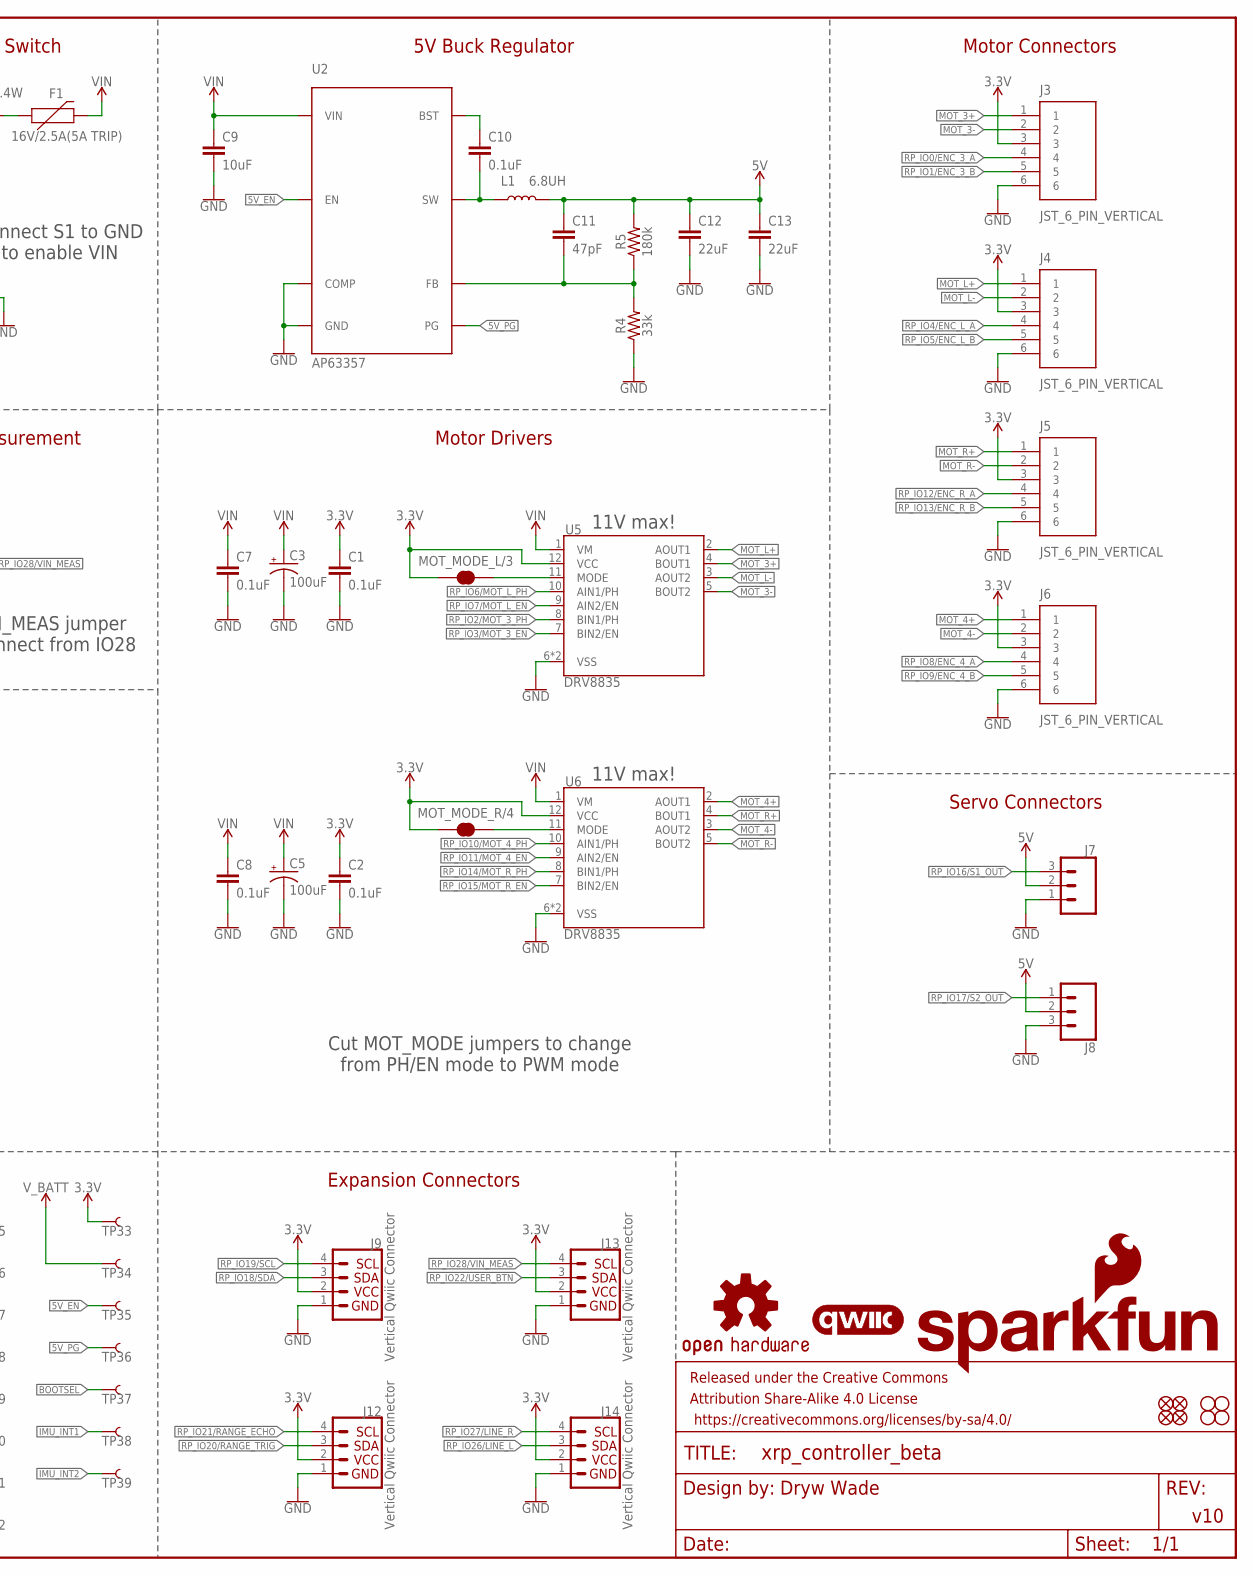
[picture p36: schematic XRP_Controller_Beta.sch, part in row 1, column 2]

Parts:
C1, C2, C4, C6, C7, C8, C10, C14, C15: 0.1uF; 0603
C3, C5: 100uF; PANASONIC_D
C9: 10uF; 0805
C11: 47pF; 0603
C12, C13: 22uF; 0805
D1, D2: Red; LED-0603
F1: 16V/2.5A(5A TRIP); 1812
FD1, FD2, FD3, FD4: FIDUCIAL1X2; FIDUCIAL-1X2
FRAME1: FRAME-LEDGER; CREATIVE_COMMONS
H1, H2, H3, H4: STAND-OFF
I2C: JUMPER-SMT_3_2-NC_TRACE_SILK; SMT-JUMPER_3_2-NC_TRACE_SILK
IMU_ADR: JUMPER-SMT_2_NC_TRACE_SILK; SMT-JUMPER_2_NC_TRACE_SILK
J1: POWER_JACKPOWER_JACK_SLOT; POWER_JACK_PTH_SLOT
J3, J4, J5, J6: JST_6_PIN_VERTICAL; JST-6-SMD-VERT-1.0MM
J7, J8: CONN_03LOCK_NO_SILK; 1X03_LOCK_NO_SILK
J9, J12, J13, J14: Vertical Qwiic Connector; JST04_1MM_VERT
L1: 6.8UH; 07A7_6U8H
LOGO1: OSHW-LOGOS; OSHW-LOGO-S
LOGO3: SFE_LOGO_NAME_FLAME.3_INCH; SFE_LOGO_NAME_FLAME_.3
MOT_MODE_L/3: JUMPER-SMT_2_NC_TRACE_SILK; SMT-JUMPER_2_NC_TRACE_SILK
MOT_MODE_R/4: JUMPER-SMT_2_NC_TRACE_SILK; SMT-JUMPER_2_NC_TRACE_SILK
MOT_PWR: JUMPER-SMT_2_NC_TRACE_SILK; SMT-JUMPER_2_NC_TRACE_SILK
Q1, Q2, Q7: TRANS_PNP_DUALSOT-363; SOT363_PHILIPS
Q3, Q4, Q5, Q6: 20V/4.2A/52mΩ/1.4W; SOT23-3
R1, R2: 2.2k; 0603
R3, R6, R7, R9, R12, R13, R16, R17: 100k; 0603
R4, R15: 33k; 0603
R5: 180k; 0603
R8: 4.7k; 0603
R10, R11, R14: 1M; 0603
R18, R19: 10; 1206
R20: 10k; 0603
RESET: MOMENTARY-SWITCH-SPST-SMD-4.6X2.8MM; TACTILE_SWITCH_SMD_4.6X2.8MM
S1: SWITCH-SPDT-SMD-RIGHT-ANGLE; SWITCH_SPST_SMD_A
SYS_PWR: JUMPER-SMT_2_NC_TRACE_SILK; SMT-JUMPER_2_NC_TRACE_SILK
TP1, TP2, TP3, TP4, TP5, TP6, TP7, TP8, TP9, TP10, TP11, TP12, TP13, TP14, TP15, TP16, TP17, TP18, TP19, TP20, TP21, TP22, TP23, TP24, TP25, TP26, TP27, TP28, TP29, TP30, TP31, TP32, TP33, TP34, TP35, TP36, TP37, TP38, TP39: TEST-POINT3X5; PAD.03X.05
U1: RPI_PICO_W_XRP; RPI_PICO_W
U2: AP63357; V-DFN3020-13
U4: LSM6DSOX; LGA14L
U5, U6: DRV8835; WSON-12
U$98: QWIIC_LOGO_5MM_INVERTED; QWIIC_5MM_INVERTED
USER: MOMENTARY-SWITCH-SPST-SMD-4.6X2.8MM; TACTILE_SWITCH_SMD_4.6X2.8MM
USER_BTN: JUMPER-SMT_2_NC_TRACE_SILK; SMT-JUMPER_2_NC_TRACE_SILK
VIN_MEAS: JUMPER-SMT_2_NC_TRACE_SILK; SMT-JUMPER_2_NC_TRACE_SILK
VUSB: JUMPER-SMT_2_NC_TRACE_SILK; SMT-JUMPER_2_NC_TRACE_SILK

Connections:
3.3V: C1.1, C2.1, C4.1, C6.1, D1.A, I2C.2, IMU_ADR.2, J3.3, J4.3, J5.3, J6.3, J9.2, J12.2, J13.2, J14.2, MOT_MODE_L/3.2, MOT_MODE_R/4.2, R17.2, TP33.1, U1.36 (3V3), U4.5 (VDDIO), U4.8 (VDD), U5.12 (VCC), U6.12 (VCC)
5V: C11.1, C12.1, C13.1, D2.A, J7.2, J8.2, L1.P$2 (2), Q5.3 (D), Q7.1 (E), R5.2
5V_EN: TP35.1, U2.P$2 (EN)
5V_PG: TP36.1, U2.P$5 (PG)
!POW_EN!: R13.1, S1.2
!RP_RESET!: C14.1, RESET.3 (2), RESET.4 (2), U1.30 (RUN)
BOOTSEL: TP37.1, U1.46 (TP_BOOTSEL)
FB: C11.2, R4.2, R5.1, U2.P$3 (FB)
GND: C1.2, C2.2, C3.-, C4.2, C5.-, C6.2, C7.2, C8.2, C9.2, C12.2, C13.2, C14.2, C15.2, J1.GND, J3.6, J4.6, J5.6, J6.6, J7.1, J8.3, J9.1, J12.1, J13.1, J14.1, MOT_PWR.1, R3.1, R4.1, R6.1, R7.1, R9.1, R10.1, R11.1, R14.1, R15.1, RESET.1, RESET.2 (1), S1.3 (S), SYS_PWR.1, U1.3 (GND), U1.8 (GND), U1.13 (GND), U1.18 (GND), U1.23 (GND), U1.28 (GND), U1.33 (AGND), U1.38 (GND), U1.41 (GND), U1.48 (GND), U1.A (GND), U1.B (GND), U1.C (GND), U1.D (GND), U2.P$4 (COMP), U2.P$8 (GND), U4.2 (SDIX), U4.3 (SCX), U4.6 (GND), U4.7 (GND), U5.6 (VSS), U5.PAD (VSS), U6.6 (VSS), U6.PAD (VSS), USER.1, USER.2 (1)
IMU_INT1: TP38.1, U4.4 (INT1)
IMU_INT2: TP39.1, U4.9 (INT2)
MOT_3+: J3.1, TP25.1, U5.4 (BOUT1)
MOT_3-: J3.2, TP26.1, U5.5 (BOUT2)
MOT_4+: J6.1, TP29.1, U6.2 (AOUT1)
MOT_4-: J6.2, TP31.1, U6.3 (AOUT2)
MOT_L+: J4.1, TP27.1, U5.2 (AOUT1)
MOT_L-: J4.2, TP28.1, U5.3 (AOUT2)
MOT_R+: J5.1, TP30.1, U6.4 (BOUT1)
MOT_R-: J5.2, TP32.1, U6.5 (BOUT2)
unnamed: D1.C, R8.2
unnamed: IMU_ADR.1, R3.2, U4.1 (SDO/SA0)
unnamed: I2C.3, R1.2
unnamed: I2C.1, R2.1
unnamed: C10.1, U2.P$6 (BST)
unnamed: Q1.2 (B), Q1.5 (B), Q1.6 (C), R6.2
unnamed: Q1.3 (C), Q3.1 (G), R10.2
unnamed: F1.1, Q6.3 (D)
unnamed: U1.40 (VBUS), VUSB.2
unnamed: R8.1, SYS_PWR.2
unnamed: Q2.2 (B), Q2.5 (B), Q2.6 (C), R9.2
unnamed: R15.2, R16.1, VIN_MEAS.2
unnamed: MOT_MODE_L/3.1, U5.11 (MODE)
unnamed: MOT_MODE_R/4.1, U6.11 (MODE)
unnamed: Q6.1 (G), R12.1, R13.2
unnamed: Q2.3 (C), Q4.1 (G), R11.2
unnamed: C15.1, R17.1, USER.3 (2), USER.4 (2), USER_BTN.1
unnamed: R18.1, R19.1, VUSB.1
unnamed: Q7.2 (B), Q7.5 (B), Q7.6 (C), R7.2
unnamed: Q5.1 (G), Q7.3 (C), R14.2
unnamed: D2.C, R20.2
unnamed: MOT_PWR.2, R20.1
RP_IO0/ENC_3_A: J3.4, TP1.1, U1.1 (GPIO0)
RP_IO1/ENC_3_B: J3.5, TP2.1, U1.2 (GPIO1)
RP_IO2/MOT_3_PH: TP3.1, U1.4 (GPIO2), U5.8 (BIN1/PH)
RP_IO3/MOT_3_EN: TP4.1, U1.5 (GPIO3), U5.7 (BIN2/EN)
RP_IO4/ENC_L_A: J4.4, TP5.1, U1.6 (GPIO4)
RP_IO5/ENC_L_B: J4.5, TP6.1, U1.7 (GPIO5)
RP_IO6/MOT_L_PH: TP7.1, U1.9 (GPIO6), U5.10 (AIN1/PH)
RP_IO7/MOT_L_EN: TP8.1, U1.10 (GPIO7), U5.9 (AIN2/EN)
RP_IO8/ENC_4_A: J6.4, TP9.1, U1.11 (GPIO8)
RP_IO9/ENC_4_B: J6.5, TP10.1, U1.12 (GPIO9)
RP_IO10/MOT_4_PH: TP11.1, U1.14 (GPIO10), U6.10 (AIN1/PH)
RP_IO11/MOT_4_EN: TP12.1, U1.15 (GPIO11), U6.9 (AIN2/EN)
RP_IO12/ENC_R_A: J5.4, TP13.1, U1.16 (GPIO12)
RP_IO13/ENC_R_B: J5.5, TP14.1, U1.17 (GPIO13)
RP_IO14/MOT_R_PH: TP15.1, U1.19 (GPIO14), U6.8 (BIN1/PH)
RP_IO15/MOT_R_EN: TP16.1, U1.20 (GPIO15), U6.7 (BIN2/EN)
RP_IO16/S1_OUT: J7.3, U1.21 (GPIO16)
RP_IO17/S2_OUT: J8.1, U1.22 (GPIO17)
RP_IO18/SDA: J9.3, R1.1, TP17.1, U1.24 (GPIO18), U4.14 (SDA)
RP_IO19/SCL: J9.4, R2.2, TP18.1, U1.25 (GPIO19), U4.13 (SCL)
RP_IO20/RANGE_TRIG: J12.3, TP19.1, U1.26 (GPIO20)
RP_IO21/RANGE_ECHO: J12.4, TP20.1, U1.27 (GPIO21)
RP_IO22/USER_BTN: J13.3, TP21.1, U1.29 (GPIO22), USER_BTN.2
RP_IO26/LINE_L: J14.3, TP22.1, U1.31 (GPIO26/ADC0)
RP_IO27/LINE_R: J14.4, TP23.1, U1.32 (GPIO27/ADC1)
RP_IO28/VIN_MEAS: J13.4, TP24.1, U1.34 (GPIO28/ADC2), VIN_MEAS.1
SW: C10.2, L1.P$1 (1), U2.P$7 (SW), U2.P$9 (SW)
VIN: C3.+, C5.+, C7.1, C8.1, C9.1, F1.2, R16.2, U2.P$1 (VIN), U5.1 (VM), U6.1 (VM)
V_BATT: J1.PWR, Q1.1 (E), Q3.3 (D), TP34.1
V_POW: Q1.4 (E), Q2.4 (E), Q3.2 (S), Q4.2 (S), Q6.2 (S), R12.2
V_SYS: Q5.2 (S), Q7.4 (E), U1.39 (VSYS)
V_USB: Q2.1 (E), Q4.3 (D), R18.2, R19.2

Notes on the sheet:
Dryw Wade
v10
Motor Connectors
Servo Connectors
Expansion Connectors
Battery Connector
Motor Drivers
RPi Pico W
6-DoF IMU
Power LED
Reset Button
11V max!
5V Buck Regulator
Power Flow Perfect Diode Circuits
Power Switch
I2C Pullups
Cut I2C jumper to remove pullup resistors
Default I2C address: 0x6B Open IMU_ADR jumper: 0x6A
Cut PWR jumpers to remove power LEDs
Cut VUSB jumper to prevent motors and servos from being powered by USB
Cut MOT_MODE jumpers to change from PH/EN mode to PWM mode
Connect S1 to GND to enable VIN
Test Points
VIN Measurement
Cut VIN_MEAS jumper to disconnect from IO28
User Button
Cut USER_BTN jumper to disconnect from IO22
V_SYS: 5.5V max!

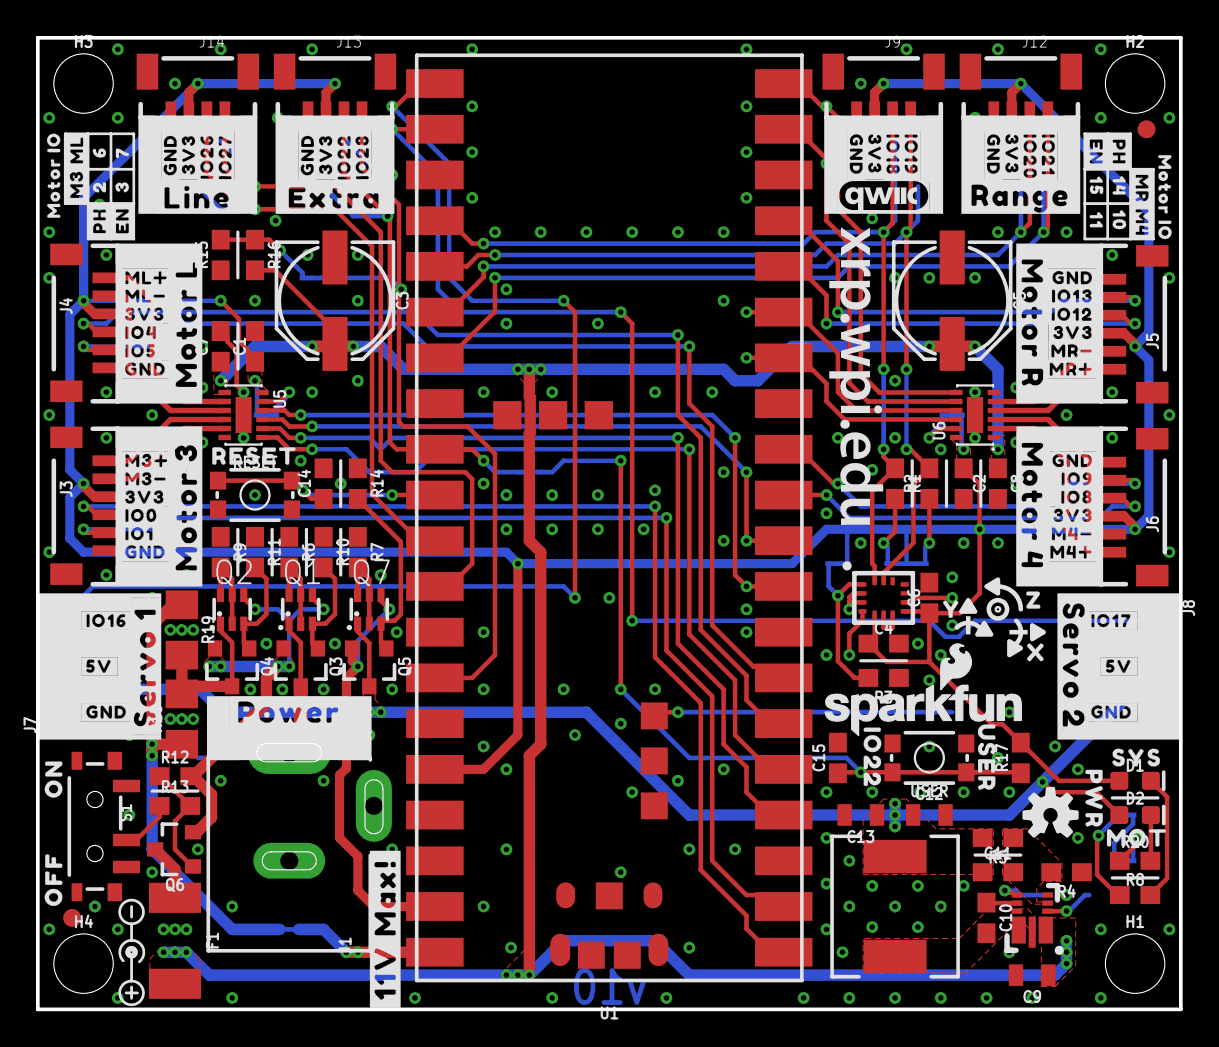
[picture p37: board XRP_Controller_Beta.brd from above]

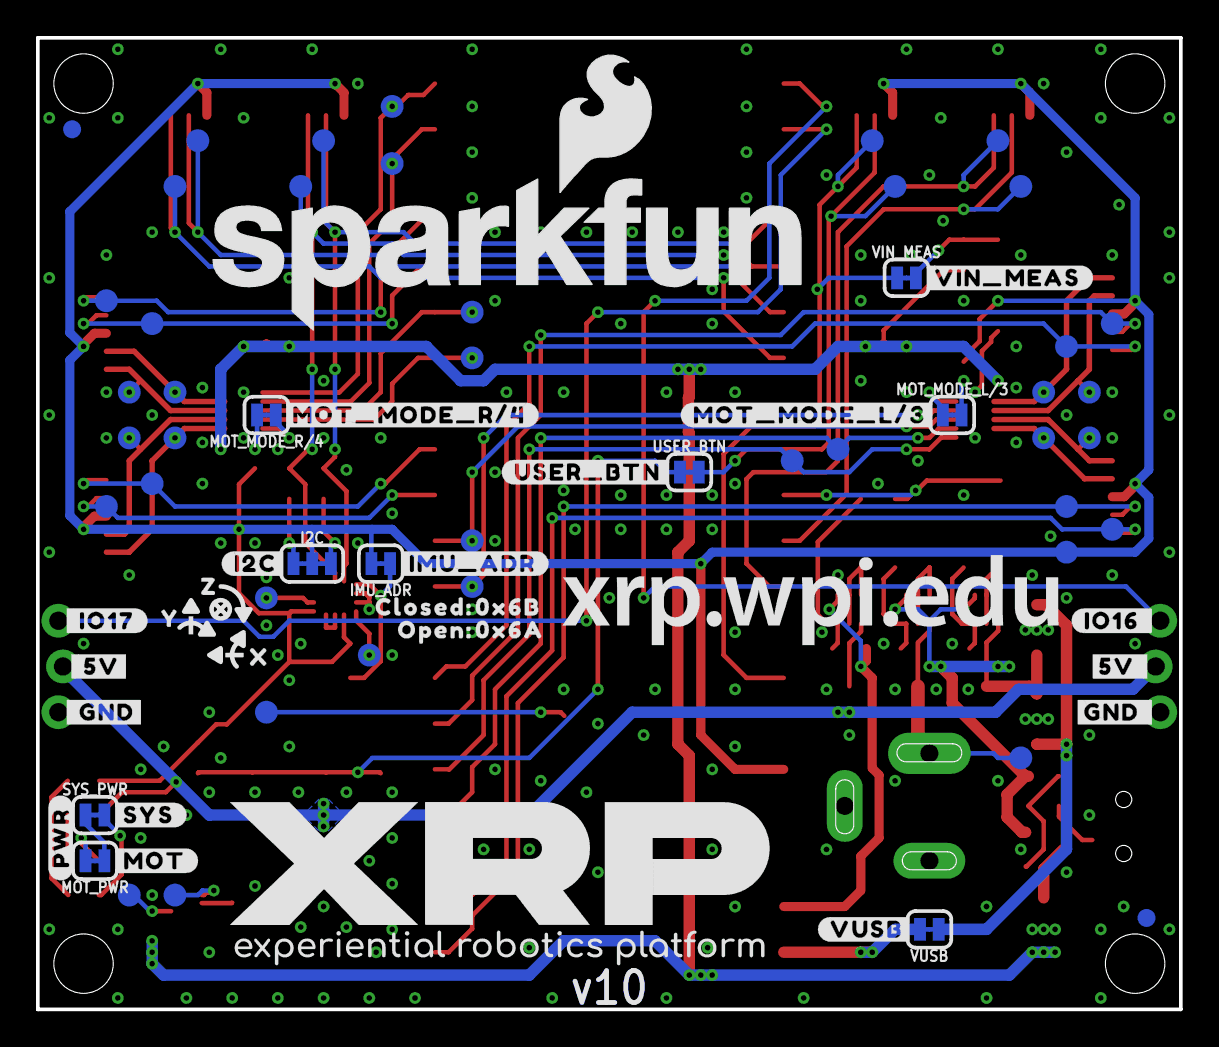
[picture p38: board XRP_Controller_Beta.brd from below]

Board: 2 copper layers, 63.5 x 54.0 mm, 240 parts (76 on the bottom side), 73 nets.

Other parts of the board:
LOGO4: SFE_LOGO_NAME_FLAME.1_INCH; SFE_LOGO_NAME_FLAME_.1
U$1: #MOTOR_3#0
U$2: #SERVO_2#0
U$3: #11V_MAX###0
U$4, U$24, U$50, U$52, U$54: #GND#0
U$5: #POWER#0
U$6: PWR0
U$7: RESET0
U$8: #MOTOR_R#0
U$9: #MR##0
U$10: #MOTOR_L#0
U$11: #SERVO_1#0
U$12: #MOTOR_4#0
U$13: #VIN_MEAS#0
U$14: #MR##1
U$15, U$25, U$51, U$53: #3V3#0
U$16: #ML##0
U$17, U$33, U$41, U$43: #3V3#4
U$18: #M4##0
U$19: #M4##5
U$20: #IO0#0
U$21: #IO1#0
U$22: #IO5#0
U$23: #IO4#0
U$26: #GND_#0
U$27: #5V_#0
U$28: #IO8#0
U$29: #IO9#0
U$30, U$31, U$40, U$42, U$57: #GND#10
U$32: #ML##1
U$34: #IO12#0
U$35: #IO13#0
U$36: ORDERING_INSTRUCTIONS
U$37, U$117: #PH#0
U$38: #IO27#0
U$39: #IO28#0
U$44: #IO26#0
U$45: #IO22#0
U$46: #IO18#0
U$47: #IO19#0
U$48: #IO20#0
U$49: #IO21#0
U$55: #5V#0
U$56: #IO16#0
U$58: #IO17#0
U$59: #5V#18
U$60: #I2C#0
U$61: #IO16_#0
U$62: ON0
U$63: OFF0
U$64: #IMU_ADR#0
U$65, U$116: #EN#0
U$66: #MOT_MODE_L#3#0
U$67: SYS0
U$68: IO220
U$69: #RANGE#0
U$70: #MOT_MODE_R#4#0
U$71: MOT0
U$72: XRP_URL_3MM
U$73: #PWR#0
U$74: #LINE#0
U$75: #_GND#0
U$76: #_5V#0
U$77: #_IO17#0
U$78: POLARITY_MARKING_CENTER_POSITIVE#JPG
U$79, U$88: X0
U$80, U$89: Y0
U$81, U$90: Z0
U$82: #EXTRA#0
U$83: USER0
U$84: #USER_BTN#0
U$85: 0X6B0
U$86: 0X6A0
U$87: OPEN#0
U$91: CLOSED#0
U$92: XRP_FULL_LOGO
U$93: #VUSB#0
U$94: #M3##0
U$95: #MOT#0
U$96: #SYS#0
U$97: XRP_URL_5MM
U$99: #M3##4
U$100: #ML#0
U$101: #M3#0
U$102: 100
U$103: 110
U$104: 140
U$105: 150
U$106: #MR#0
U$107: #M4#0
U$108: 20
U$109: 30
U$110: 60
U$111: 70
U$114, U$115: MOTOR_IO0

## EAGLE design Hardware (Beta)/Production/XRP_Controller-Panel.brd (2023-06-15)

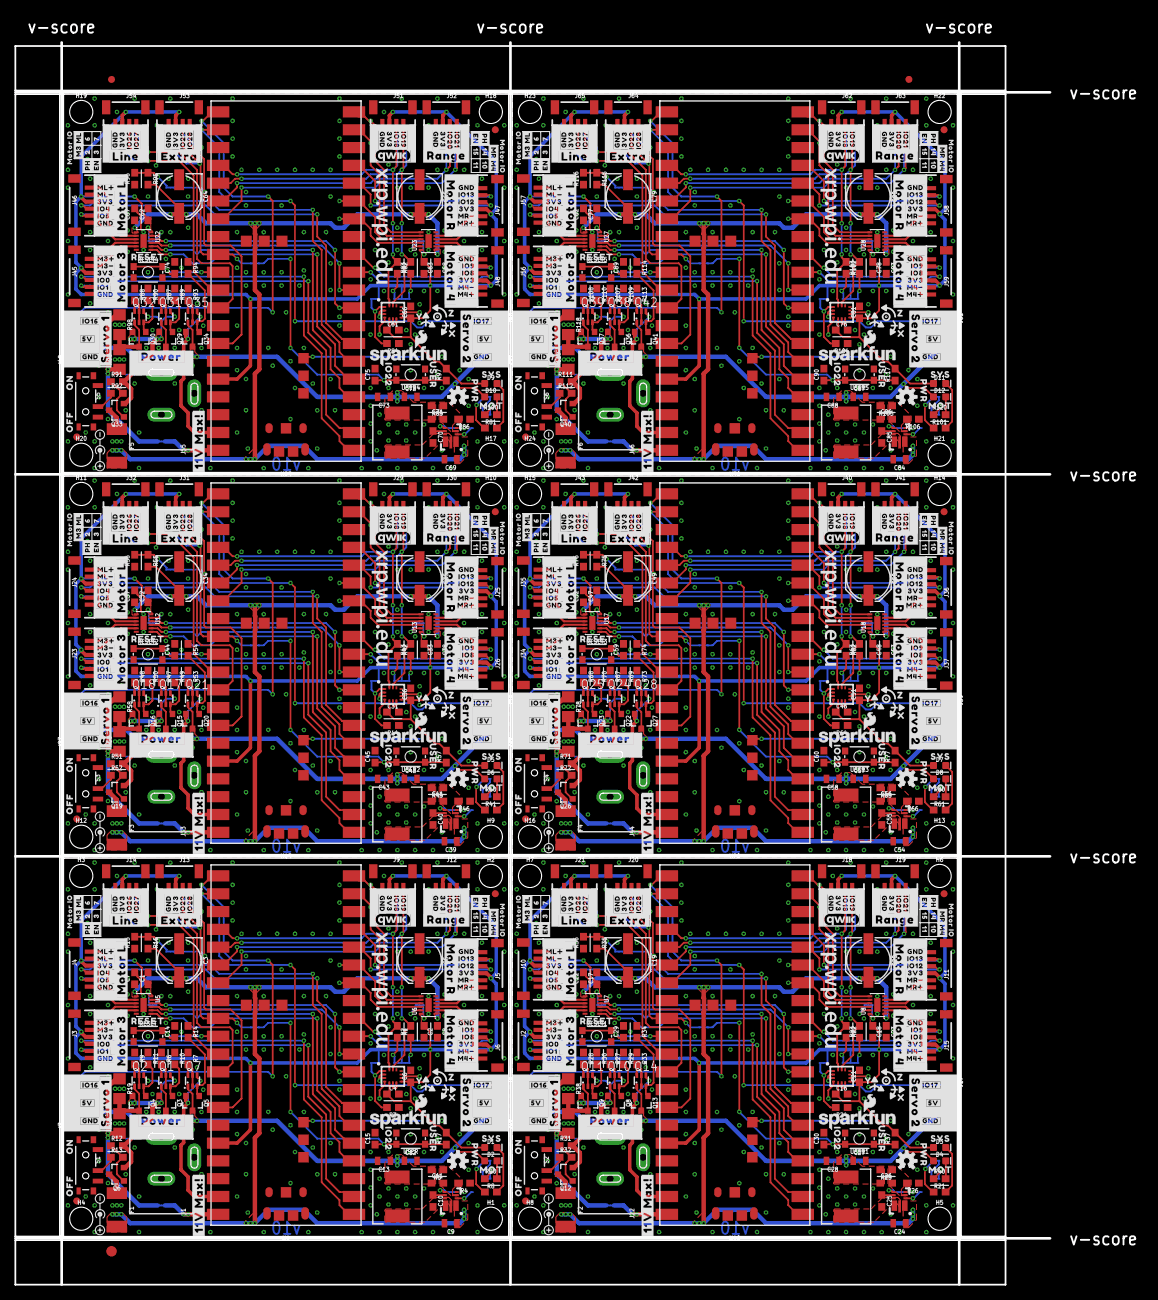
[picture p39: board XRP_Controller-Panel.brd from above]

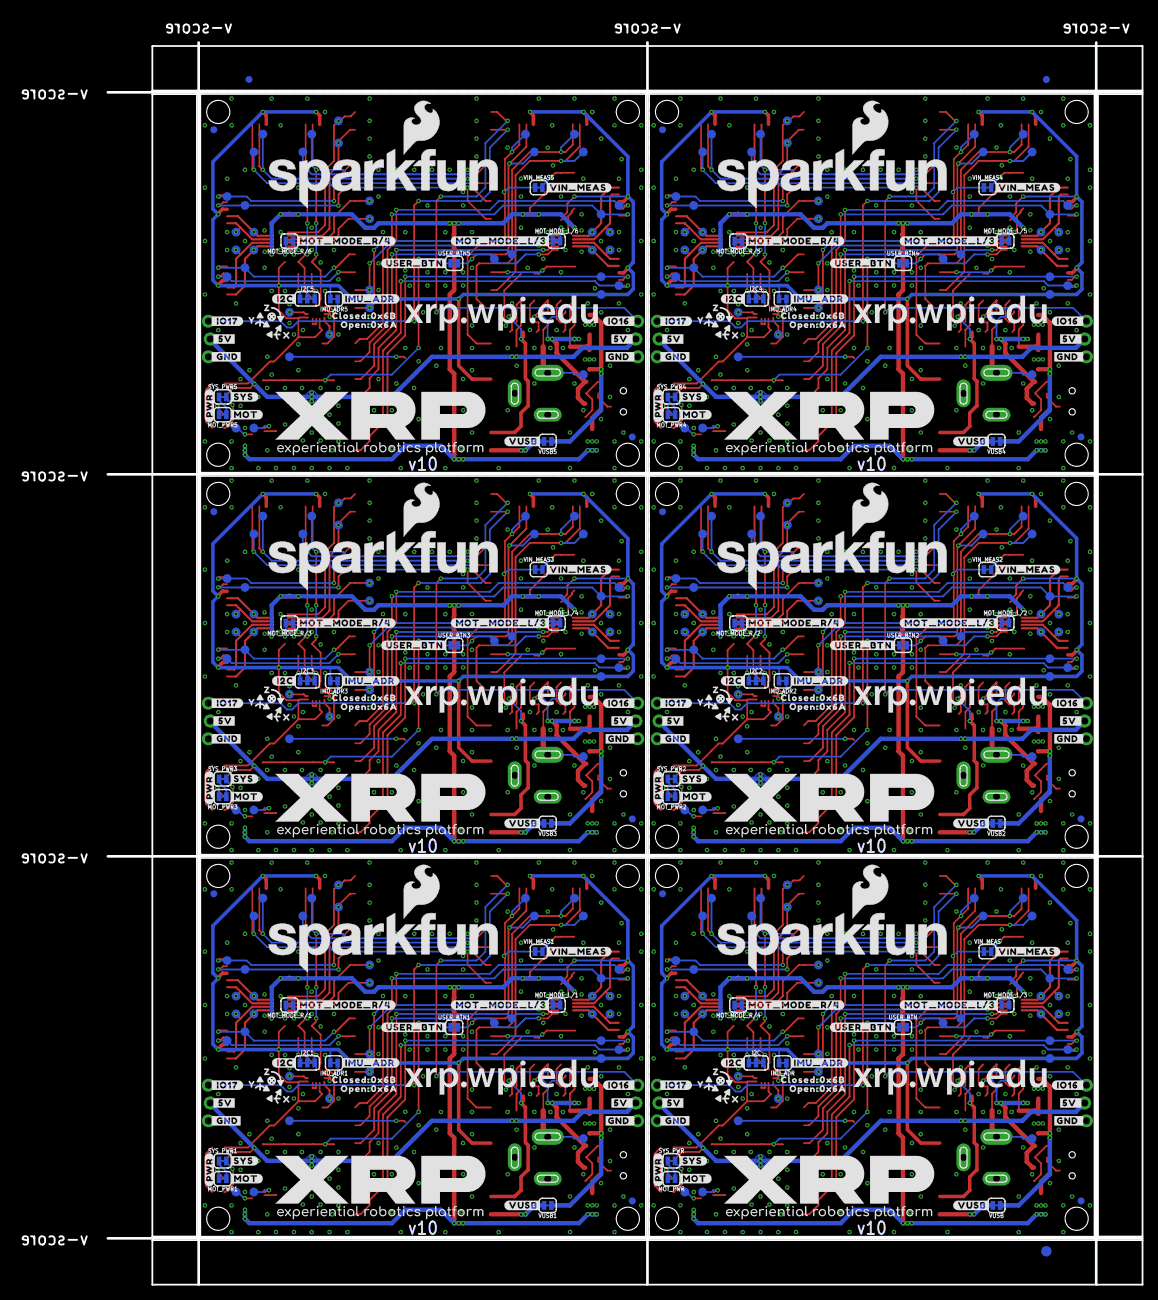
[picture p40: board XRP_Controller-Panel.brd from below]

Board: 2 copper layers, 147.6 x 177.2 mm, 1434 parts (459 on the bottom side), 438 nets.

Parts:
C1, C2, C4, C6, C7, C8, C10, C14, C15, C16, C17, C18, C21, C22, C23, C25, C29, C30, C31, C32, C33, C36, C37, C38, C40, C44, C45, C46, C47, C48, C51, C52, C53, C55, C59, C60, C61, C62, C63, C66, C67, C68, C70, C74, C75, C76, C77, C78, C81, C82, C83, C85, C89, C90: 0.1uF; 0603
C3, C5, C19, C20, C34, C35, C49, C50, C64, C65, C79, C80: 100uF; PANASONIC_D
C9, C24, C39, C54, C69, C84: 10uF; 0805
C11, C26, C41, C56, C71, C86: 47pF; 0603
C12, C13, C27, C28, C42, C43, C57, C58, C72, C73, C87, C88: 22uF; 0805
D1, D2, D3, D4, D5, D6, D7, D8, D9, D10, D11, D12: Red; LED-0603
E$1, E$2, E$3, E$4: FIDUCIAL-1X2
E$5, E$6: FIDUCIAL-1.5X3
F1, F2, F3, F4, F5, F6: 16V/2.5A(5A TRIP); 1812
FD1, FD2, FD3, FD4, FD5, FD6, FD7, FD8, FD9, FD10, FD11, FD12, FD13, FD14, FD15, FD16, FD17, FD18, FD19, FD20, FD21, FD22, FD23, FD24: FIDUCIAL1X2; FIDUCIAL-1X2
H1, H2, H3, H4, H5, H6, H7, H8, H9, H10, H11, H12, H13, H14, H15, H16, H17, H18, H19, H20, H21, H22, H23, H24: STAND-OFF
I2C, I2C1, I2C2, I2C3, I2C4, I2C5: JUMPER-SMT_3_2-NC_TRACE_SILK; SMT-JUMPER_3_2-NC_TRACE_SILK
IMU_ADR, IMU_ADR1, IMU_ADR2, IMU_ADR3, IMU_ADR4, IMU_ADR5: JUMPER-SMT_2_NC_TRACE_SILK; SMT-JUMPER_2_NC_TRACE_SILK
J1, J22, J33, J44, J55, J66: POWER_JACKPOWER_JACK_SLOT; POWER_JACK_PTH_SLOT
J2, J3, J4, J5, J6, J10, J11, J15, J23, J24, J25, J26, J34, J35, J36, J37, J45, J46, J47, J48, J56, J57, J58, J59: JST_6_PIN_VERTICAL; JST-6-SMD-VERT-1.0MM
J7, J8, J16, J17, J27, J28, J38, J39, J49, J50, J60, J61: 1X03_LOCK_NO_SILK
J9, J12, J13, J14, J18, J19, J20, J21, J29, J30, J31, J32, J40, J41, J42, J43, J51, J52, J53, J54, J62, J63, J64, J65: Vertical Qwiic Connector; JST04_1MM_VERT
L1, L2, L3, L4, L5, L6: 6.8UH; 07A7_6U8H
LOGO1, LOGO2, LOGO7, LOGO10, LOGO13, LOGO16: OSHW-LOGOS; OSHW-LOGO-S
LOGO3, LOGO5, LOGO8, LOGO11, LOGO14, LOGO17: SFE_LOGO_NAME_FLAME.3_INCH; SFE_LOGO_NAME_FLAME_.3
LOGO4, LOGO6, LOGO9, LOGO12, LOGO15, LOGO18: SFE_LOGO_NAME_FLAME.1_INCH; SFE_LOGO_NAME_FLAME_.1
MOT_MODE_L/1, MOT_MODE_L/2, MOT_MODE_L/3, MOT_MODE_L/4, MOT_MODE_L/5, MOT_MODE_L/6: JUMPER-SMT_2_NC_TRACE_SILK; SMT-JUMPER_2_NC_TRACE_SILK
MOT_MODE_R/1, MOT_MODE_R/2, MOT_MODE_R/3, MOT_MODE_R/4, MOT_MODE_R/5, MOT_MODE_R/6: JUMPER-SMT_2_NC_TRACE_SILK; SMT-JUMPER_2_NC_TRACE_SILK
MOT_PWR, MOT_PWR1, MOT_PWR2, MOT_PWR3, MOT_PWR4, MOT_PWR5: JUMPER-SMT_2_NC_TRACE_SILK; SMT-JUMPER_2_NC_TRACE_SILK
Q1, Q2, Q7, Q10, Q11, Q14, Q17, Q18, Q21, Q24, Q25, Q28, Q31, Q32, Q35, Q38, Q39, Q42: SOT363_PHILIPS
Q3, Q4, Q5, Q6, Q8, Q9, Q12, Q13, Q15, Q16, Q19, Q20, Q22, Q23, Q26, Q27, Q29, Q30, Q33, Q34, Q36, Q37, Q40, Q41: 20V/4.2A/52mΩ/1.4W; SOT23-3
R1, R2, R22, R23, R42, R43, R62, R63, R82, R83, R102, R103: 2.2k; 0603
R3, R6, R7, R9, R12, R13, R16, R17, R24, R27, R28, R31, R32, R33, R35, R37, R44, R47, R48, R51, R52, R53, R55, R57, R64, R67, R68, R71, R72, R73, R75, R77, R84, R87, R88, R91, R92, R93, R95, R97, R104, R107, R108, R111, R112, R113, R115, R117: 100k; 0603
R4, R15, R26, R36, R46, R56, R66, R76, R86, R96, R106, R116: 33k; 0603
R5, R25, R45, R65, R85, R105: 180k; 0603
R8, R21, R41, R61, R81, R101: 4.7k; 0603
R10, R11, R14, R29, R30, R34, R49, R50, R54, R69, R70, R74, R89, R90, R94, R109, R110, R114: 1M; 0603
R18, R19, R38, R39, R58, R59, R78, R79, R98, R99, R118, R119: 10; 1206
R20, R40, R60, R80, R100, R120: 10k; 0603
RESET, RESET1, RESET2, RESET3, RESET4, RESET5: MOMENTARY-SWITCH-SPST-SMD-4.6X2.8MM; TACTILE_SWITCH_SMD_4.6X2.8MM
S1, S2, S3, S4, S5, S6: SWITCH_SPST_SMD_A
SYS_PWR, SYS_PWR1, SYS_PWR2, SYS_PWR3, SYS_PWR4, SYS_PWR5: JUMPER-SMT_2_NC_TRACE_SILK; SMT-JUMPER_2_NC_TRACE_SILK
TP1, TP2, TP3, TP4, TP5, TP6, TP7, TP8, TP9, TP10, TP11, TP12, TP13, TP14, TP15, TP16, TP17, TP18, TP19, TP20, TP21, TP22, TP23, TP24, TP25, TP26, TP27, TP28, TP29, TP30, TP31, TP32, TP33, TP34, TP35, TP36, TP37, TP38, TP39, TP40, TP41, TP42, TP43, TP44, TP45, TP46, TP47, TP48, TP49, TP50, TP51, TP52, TP53, TP54, TP55, TP56, TP57, TP58, TP59, TP60, TP61, TP62, TP63, TP64, TP65, TP66, TP67, TP68, TP69, TP70, TP71, TP72, TP73, TP74, TP75, TP76, TP77, TP78, TP79, TP80, TP81, TP82, TP83, TP84, TP85, TP86, TP87, TP88, TP89, TP90, TP91, TP92, TP93, TP94, TP95, TP96, TP97, TP98, TP99, TP100, TP101, TP102, TP103, TP104, TP105, TP106, TP107, TP108, TP109, TP110, TP111, TP112, TP113, TP114, TP115, TP116, TP117, TP118, TP119, TP120, TP121, TP122, TP123, TP124, TP125, TP126, TP127, TP128, TP129, TP130, TP131, TP132, TP133, TP134, TP135, TP136, TP137, TP138, TP139, TP140, TP141, TP142, TP143, TP144, TP145, TP146, TP147, TP148, TP149, TP150, TP151, TP152, TP153, TP154, TP155, TP156, TP157, TP158, TP159, TP160, TP161, TP162, TP163, TP164, TP165, TP166, TP167, TP168, TP169, TP170, TP171, TP172, TP173, TP174, TP175, TP176, TP177, TP178, TP179, TP180, TP181, TP182, TP183, TP184, TP185, TP186, TP187, TP188, TP189, TP190, TP191, TP192, TP193, TP194, TP195, TP196, TP197, TP198, TP199, TP200, TP201, TP202, TP203, TP204, TP205, TP206, TP207, TP208, TP209, TP210, TP211, TP212, TP213, TP214, TP215, TP216, TP217, TP218, TP219, TP220, TP221, TP222, TP223, TP224, TP225, TP226, TP227, TP228, TP229, TP230, TP231, TP232, TP233, TP234: TEST-POINT3X5; PAD.03X.05
U1, U10, U15, U20, U25, U30: RPI_PICO_W_XRP; RPI_PICO_W
U2, U9, U14, U19, U24, U29: AP63357; V-DFN3020-13
U3, U4, U11, U16, U21, U26: LSM6DS0X; LGA14L
U5, U6, U7, U8, U12, U13, U17, U18, U22, U23, U27, U28: DRV8835; WSON-12
U$1, U$165, U$279, U$393, U$507, U$621: #MOTOR_3#0
U$2, U$169, U$283, U$397, U$511, U$625: #SERVO_2#0
U$3, U$170, U$284, U$398, U$512, U$626: #11V_MAX###0
U$4, U$24, U$50, U$52, U$54, U$118, U$124, U$146, U$148, U$150, U$232, U$238, U$260, U$262, U$264, U$346, U$352, U$374, U$376, U$378, U$460, U$466, U$488, U$490, U$492, U$574, U$580, U$602, U$604, U$606: #GND#0
U$5, U$36, U$229, U$343, U$457, U$571: #POWER#0
U$6, U$112, U$230, U$344, U$458, U$572: PWR0
U$7, U$113, U$231, U$345, U$459, U$573: RESET0
U$8, U$167, U$281, U$395, U$509, U$623: #MOTOR_R#0
U$9, U$207, U$321, U$435, U$549, U$663: #MR##0
U$10, U$164, U$278, U$392, U$506, U$620: #MOTOR_L#0
U$11, U$166, U$280, U$394, U$508, U$622: #SERVO_1#0
U$12, U$168, U$282, U$396, U$510, U$624: #MOTOR_4#0
U$13, U$182, U$296, U$410, U$524, U$638: #VIN_MEAS#0
U$14, U$208, U$322, U$436, U$550, U$664: #MR##1
U$15, U$25, U$51, U$53, U$119, U$125, U$147, U$149, U$233, U$239, U$261, U$263, U$347, U$353, U$375, U$377, U$461, U$467, U$489, U$491, U$575, U$581, U$603, U$605: #3V3#0
U$16, U$205, U$319, U$433, U$547, U$661: #ML##0
U$17, U$33, U$41, U$43, U$129, U$131, U$137, U$139, U$243, U$245, U$251, U$253, U$357, U$359, U$365, U$367, U$471, U$473, U$479, U$481, U$585, U$587, U$593, U$595: #3V3#4
U$18, U$209, U$323, U$437, U$551, U$665: #M4##0
U$19, U$210, U$324, U$438, U$552, U$666: #M4##5
U$20, U$120, U$234, U$348, U$462, U$576: #IO0#0
U$21, U$121, U$235, U$349, U$463, U$577: #IO1#0
U$22, U$122, U$236, U$350, U$464, U$578: #IO5#0
U$23, U$123, U$237, U$351, U$465, U$579: #IO4#0
U$26, U$172, U$286, U$400, U$514, U$628: #GND_#0
U$27, U$171, U$285, U$399, U$513, U$627: #5V_#0
U$28, U$126, U$240, U$354, U$468, U$582: #IO8#0
U$29, U$127, U$241, U$355, U$469, U$583: #IO9#0
U$30, U$31, U$40, U$42, U$57, U$128, U$130, U$136, U$138, U$153, U$242, U$244, U$250, U$252, U$267, U$356, U$358, U$364, U$366, U$381, U$470, U$472, U$478, U$480, U$495, U$584, U$586, U$592, U$594, U$609: #GND#10
U$32, U$206, U$320, U$434, U$548, U$662: #ML##1
U$34, U$132, U$246, U$360, U$474, U$588: #IO12#0
U$35, U$133, U$247, U$361, U$475, U$589: #IO13#0
U$37, U$117, U$218, U$222, U$332, U$336, U$446, U$450, U$560, U$564, U$674, U$678: #PH#0
U$38, U$134, U$248, U$362, U$476, U$590: #IO27#0
U$39, U$135, U$249, U$363, U$477, U$591: #IO28#0
U$44, U$140, U$254, U$368, U$482, U$596: #IO26#0
U$45, U$141, U$255, U$369, U$483, U$597: #IO22#0
U$46, U$142, U$256, U$370, U$484, U$598: #IO18#0
U$47, U$143, U$257, U$371, U$485, U$599: #IO19#0
U$48, U$144, U$258, U$372, U$486, U$600: #IO20#0
U$49, U$145, U$259, U$373, U$487, U$601: #IO21#0
U$55, U$151, U$265, U$379, U$493, U$607: #5V#0
U$56, U$152, U$266, U$380, U$494, U$608: #IO16#0
U$58, U$154, U$268, U$382, U$496, U$610: #IO17#0
U$59, U$155, U$269, U$383, U$497, U$611: #5V#18
U$60, U$156, U$270, U$384, U$498, U$612: #I2C#0
U$61, U$173, U$287, U$401, U$515, U$629: #IO16_#0
U$62, U$157, U$271, U$385, U$499, U$613: ON0
U$63, U$158, U$272, U$386, U$500, U$614: OFF0
U$64, U$162, U$276, U$390, U$504, U$618: #IMU_ADR#0
U$65, U$116, U$217, U$221, U$331, U$335, U$445, U$449, U$559, U$563, U$673, U$677: #EN#0
U$66, U$194, U$308, U$422, U$536, U$650: #MOT_MODE_L#3#0
U$67, U$195, U$309, U$423, U$537, U$651: SYS0
U$68, U$191, U$305, U$419, U$533, U$647: IO220
U$69, U$192, U$306, U$420, U$534, U$648: #RANGE#0
U$70, U$193, U$307, U$421, U$535, U$649: #MOT_MODE_R#4#0
U$71, U$196, U$310, U$424, U$538, U$652: MOT0
U$72, U$201, U$315, U$429, U$543, U$657: XRP_URL_3MM
U$73, U$199, U$313, U$427, U$541, U$655: #PWR#0
U$74, U$163, U$277, U$391, U$505, U$619: #LINE#0
U$75, U$174, U$288, U$402, U$516, U$630: #_GND#0
U$76, U$175, U$289, U$403, U$517, U$631: #_5V#0
U$77, U$176, U$290, U$404, U$518, U$632: #_IO17#0
U$78, U$177, U$291, U$405, U$519, U$633: POLARITY_MARKING_CENTER_POSITIVE#JPG
U$79, U$88, U$159, U$178, U$273, U$292, U$387, U$406, U$501, U$520, U$615, U$634: X0
U$80, U$89, U$160, U$179, U$274, U$293, U$388, U$407, U$502, U$521, U$616, U$635: Y0
U$81, U$90, U$161, U$180, U$275, U$294, U$389, U$408, U$503, U$522, U$617, U$636: Z0
U$82, U$181, U$295, U$409, U$523, U$637: #EXTRA#0
U$83, U$183, U$297, U$411, U$525, U$639: USER0
U$84, U$184, U$298, U$412, U$526, U$640: #USER_BTN#0
U$85, U$185, U$299, U$413, U$527, U$641: 0X6B0
U$86, U$186, U$300, U$414, U$528, U$642: 0X6A0
U$87, U$187, U$301, U$415, U$529, U$643: OPEN#0
U$91, U$188, U$302, U$416, U$530, U$644: CLOSED#0
U$92, U$189, U$303, U$417, U$531, U$645: XRP_FULL_LOGO
U$93, U$190, U$304, U$418, U$532, U$646: #VUSB#0
U$94, U$203, U$317, U$431, U$545, U$659: #M3##0
U$95, U$197, U$311, U$425, U$539, U$653: #MOT#0
U$96, U$198, U$312, U$426, U$540, U$654: #SYS#0
U$97, U$202, U$316, U$430, U$544, U$658: XRP_URL_5MM
U$98, U$200, U$314, U$428, U$542, U$656: QWIIC_LOGO; QWIIC_INVERTED
U$99, U$204, U$318, U$432, U$546, U$660: #M3##4
U$100, U$219, U$333, U$447, U$561, U$675: #ML#0
U$101, U$220, U$334, U$448, U$562, U$676: #M3#0
U$102, U$211, U$325, U$439, U$553, U$667: 100
U$103, U$212, U$326, U$440, U$554, U$668: 110
U$104, U$213, U$327, U$441, U$555, U$669: 140
U$105, U$214, U$328, U$442, U$556, U$670: 150
U$106, U$224, U$338, U$452, U$566, U$680: #MR#0
U$107, U$223, U$337, U$451, U$565, U$679: #M4#0
U$108, U$225, U$339, U$453, U$567, U$681: 20
U$109, U$226, U$340, U$454, U$568, U$682: 30
U$110, U$227, U$341, U$455, U$569, U$683: 60
U$111, U$228, U$342, U$456, U$570, U$684: 70
U$114, U$115, U$215, U$216, U$329, U$330, U$443, U$444, U$557, U$558, U$671, U$672: MOTOR_IO0
USER, USER1, USER2, USER3, USER4, USER5: MOMENTARY-SWITCH-SPST-SMD-4.6X2.8MM; TACTILE_SWITCH_SMD_4.6X2.8MM
USER_BTN, USER_BTN1, USER_BTN2, USER_BTN3, USER_BTN4, USER_BTN5: JUMPER-SMT_2_NC_TRACE_SILK; SMT-JUMPER_2_NC_TRACE_SILK
VIN_MEAS, VIN_MEAS1, VIN_MEAS2, VIN_MEAS3, VIN_MEAS4, VIN_MEAS5: JUMPER-SMT_2_NC_TRACE_SILK; SMT-JUMPER_2_NC_TRACE_SILK
VUSB, VUSB1, VUSB2, VUSB3, VUSB4, VUSB5: JUMPER-SMT_2_NC_TRACE_SILK; SMT-JUMPER_2_NC_TRACE_SILK

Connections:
3.3V: C1.1, C2.1, C4.1, C6.1, D1.A, I2C.2, IMU_ADR.2, J3.3, J4.3, J5.3, J6.3, J9.2, J12.2, J13.2, J14.2, MOT_MODE_L/3.2, MOT_MODE_R/4.2, R17.2, TP33.1, U1.36, U4.5, U4.8, U5.12, U6.12
3.3V1: C16.1, C17.1, C18.1, C21.1, D3.A, I2C1.2, IMU_ADR1.2, J2.3, J10.3, J11.3, J15.3, J18.2, J19.2, J20.2, J21.2, MOT_MODE_L/1.2, MOT_MODE_R/1.2, R37.2, TP72.1, U3.5, U3.8, U7.12, U8.12, U10.36
3.3V2: C31.1, C32.1, C33.1, C36.1, D5.A, I2C2.2, IMU_ADR2.2, J23.3, J24.3, J25.3, J26.3, J29.2, J30.2, J31.2, J32.2, MOT_MODE_L/2.2, MOT_MODE_R/2.2, R57.2, TP111.1, U11.5, U11.8, U12.12, U13.12, U15.36
3.3V3: C46.1, C47.1, C48.1, C51.1, D7.A, I2C3.2, IMU_ADR3.2, J34.3, J35.3, J36.3, J37.3, J40.2, J41.2, J42.2, J43.2, MOT_MODE_L/4.2, MOT_MODE_R/3.2, R77.2, TP150.1, U16.5, U16.8, U17.12, U18.12, U20.36
3.3V4: C61.1, C62.1, C63.1, C66.1, D9.A, I2C4.2, IMU_ADR4.2, J45.3, J46.3, J47.3, J48.3, J51.2, J52.2, J53.2, J54.2, MOT_MODE_L/5.2, MOT_MODE_R/5.2, R97.2, TP189.1, U21.5, U21.8, U22.12, U23.12, U25.36
3.3V5: C76.1, C77.1, C78.1, C81.1, D11.A, I2C5.2, IMU_ADR5.2, J56.3, J57.3, J58.3, J59.3, J62.2, J63.2, J64.2, J65.2, MOT_MODE_L/6.2, MOT_MODE_R/6.2, R117.2, TP228.1, U26.5, U26.8, U27.12, U28.12, U30.36
5V: C11.1, C12.1, C13.1, D2.A, J7.2, J8.2, L1.P$2, Q5.3, Q7.1, R5.2
5V1: C26.1, C27.1, C28.1, D4.A, J16.2, J17.2, L2.P$2, Q13.3, Q14.1, R25.2
5V2: C41.1, C42.1, C43.1, D6.A, J27.2, J28.2, L3.P$2, Q20.3, Q21.1, R45.2
5V3: C56.1, C57.1, C58.1, D8.A, J38.2, J39.2, L4.P$2, Q27.3, Q28.1, R65.2
5V4: C71.1, C72.1, C73.1, D10.A, J49.2, J50.2, L5.P$2, Q34.3, Q35.1, R85.2
5V5: C86.1, C87.1, C88.1, D12.A, J60.2, J61.2, L6.P$2, Q41.3, Q42.1, R105.2
5V_EN: TP35.1, U2.P$2
5V_EN1: TP73.1, U9.P$2
5V_EN2: TP112.1, U14.P$2
5V_EN3: TP151.1, U19.P$2
5V_EN4: TP190.1, U24.P$2
5V_EN5: TP229.1, U29.P$2
5V_PG: TP36.1, U2.P$5
5V_PG1: TP74.1, U9.P$5
5V_PG2: TP113.1, U14.P$5
5V_PG3: TP152.1, U19.P$5
5V_PG4: TP191.1, U24.P$5
5V_PG5: TP230.1, U29.P$5
!POW_EN!: R13.1, S1.2
!POW_EN!1: R32.1, S2.2
!POW_EN!2: R52.1, S3.2
!POW_EN!3: R72.1, S4.2
!POW_EN!4: R92.1, S5.2
!POW_EN!5: R112.1, S6.2
!RP_RESET!: C14.1, RESET.3, RESET.4, U1.30
!RP_RESET!1: C29.1, RESET1.3, RESET1.4, U10.30
!RP_RESET!2: C44.1, RESET2.3, RESET2.4, U15.30
!RP_RESET!3: C59.1, RESET3.3, RESET3.4, U20.30
!RP_RESET!4: C74.1, RESET4.3, RESET4.4, U25.30
!RP_RESET!5: C89.1, RESET5.3, RESET5.4, U30.30
BOOTSEL: TP37.1, U1.46
BOOTSEL1: TP75.1, U10.46
BOOTSEL2: TP114.1, U15.46
BOOTSEL3: TP153.1, U20.46
BOOTSEL4: TP192.1, U25.46
BOOTSEL5: TP231.1, U30.46
FB: C11.2, R4.2, R5.1, U2.P$3
FB1: C26.2, R25.1, R26.2, U9.P$3
FB2: C41.2, R45.1, R46.2, U14.P$3
FB3: C56.2, R65.1, R66.2, U19.P$3
FB4: C71.2, R85.1, R86.2, U24.P$3
FB5: C86.2, R105.1, R106.2, U29.P$3
GND: C1.2, C2.2, C3.-, C4.2, C5.-, C6.2, C7.2, C8.2, C9.2, C12.2, C13.2, C14.2, C15.2, J1.GND, J3.6, J4.6, J5.6, J6.6, J7.1, J8.3, J9.1, J12.1, J13.1, J14.1, MOT_PWR.1, R3.1, R4.1, R6.1, R7.1, R9.1, R10.1, R11.1, R14.1, R15.1, RESET.1, RESET.2, S1.3, SYS_PWR.1, U1.3, U1.8, U1.13, U1.18, U1.23, U1.28, U1.33, U1.38, U1.41, U1.48, U1.A, U1.B, U1.C, U1.D, U2.P$4, U2.P$8, U4.2, U4.3, U4.6, U4.7, U5.6, U5.PAD, U6.6, U6.PAD, USER.1, USER.2
GND1: C16.2, C17.2, C18.2, C19.-, C20.-, C21.2, C22.2, C23.2, C24.2, C27.2, C28.2, C29.2, C30.2, J2.6, J10.6, J11.6, J15.6, J16.1, J17.3, J18.1, J19.1, J20.1, J21.1, J22.GND, MOT_PWR1.1, R24.1, R26.1, R27.1, R28.1, R29.1, R30.1, R33.1, R34.1, R36.1, RESET1.1, RESET1.2, S2.3, SYS_PWR1.1, U3.2, U3.3, U3.6, U3.7, U7.6, U7.PAD, U8.6, U8.PAD, U9.P$4, U9.P$8, U10.3, U10.8, U10.13, U10.18, U10.23, U10.28, U10.33, U10.38, U10.41, U10.48, U10.A, U10.B, U10.C, U10.D, USER1.1, USER1.2
GND2: C31.2, C32.2, C33.2, C34.-, C35.-, C36.2, C37.2, C38.2, C39.2, C42.2, C43.2, C44.2, C45.2, J23.6, J24.6, J25.6, J26.6, J27.1, J28.3, J29.1, J30.1, J31.1, J32.1, J33.GND, MOT_PWR2.1, R44.1, R46.1, R47.1, R48.1, R49.1, R50.1, R53.1, R54.1, R56.1, RESET2.1, RESET2.2, S3.3, SYS_PWR2.1, U11.2, U11.3, U11.6, U11.7, U12.6, U12.PAD, U13.6, U13.PAD, U14.P$4, U14.P$8, U15.3, U15.8, U15.13, U15.18, U15.23, U15.28, U15.33, U15.38, U15.41, U15.48, U15.A, U15.B, U15.C, U15.D, USER2.1, USER2.2
GND3: C46.2, C47.2, C48.2, C49.-, C50.-, C51.2, C52.2, C53.2, C54.2, C57.2, C58.2, C59.2, C60.2, J34.6, J35.6, J36.6, J37.6, J38.1, J39.3, J40.1, J41.1, J42.1, J43.1, J44.GND, MOT_PWR3.1, R64.1, R66.1, R67.1, R68.1, R69.1, R70.1, R73.1, R74.1, R76.1, RESET3.1, RESET3.2, S4.3, SYS_PWR3.1, U16.2, U16.3, U16.6, U16.7, U17.6, U17.PAD, U18.6, U18.PAD, U19.P$4, U19.P$8, U20.3, U20.8, U20.13, U20.18, U20.23, U20.28, U20.33, U20.38, U20.41, U20.48, U20.A, U20.B, U20.C, U20.D, USER3.1, USER3.2
GND4: C61.2, C62.2, C63.2, C64.-, C65.-, C66.2, C67.2, C68.2, C69.2, C72.2, C73.2, C74.2, C75.2, J45.6, J46.6, J47.6, J48.6, J49.1, J50.3, J51.1, J52.1, J53.1, J54.1, J55.GND, MOT_PWR4.1, R84.1, R86.1, R87.1, R88.1, R89.1, R90.1, R93.1, R94.1, R96.1, RESET4.1, RESET4.2, S5.3, SYS_PWR4.1, U21.2, U21.3, U21.6, U21.7, U22.6, U22.PAD, U23.6, U23.PAD, U24.P$4, U24.P$8, U25.3, U25.8, U25.13, U25.18, U25.23, U25.28, U25.33, U25.38, U25.41, U25.48, U25.A, U25.B, U25.C, U25.D, USER4.1, USER4.2
GND5: C76.2, C77.2, C78.2, C79.-, C80.-, C81.2, C82.2, C83.2, C84.2, C87.2, C88.2, C89.2, C90.2, J56.6, J57.6, J58.6, J59.6, J60.1, J61.3, J62.1, J63.1, J64.1, J65.1, J66.GND, MOT_PWR5.1, R104.1, R106.1, R107.1, R108.1, R109.1, R110.1, R113.1, R114.1, R116.1, RESET5.1, RESET5.2, S6.3, SYS_PWR5.1, U26.2, U26.3, U26.6, U26.7, U27.6, U27.PAD, U28.6, U28.PAD, U29.P$4, U29.P$8, U30.3, U30.8, U30.13, U30.18, U30.23, U30.28, U30.33, U30.38, U30.41, U30.48, U30.A, U30.B, U30.C, U30.D, USER5.1, USER5.2
IMU_INT1: TP38.1, U4.4
IMU_INT2: TP39.1, U4.9
IMU_INT3: TP77.1, U3.9
IMU_INT4: TP78.1, U3.4
IMU_INT5: TP116.1, U11.9
IMU_INT6: TP117.1, U11.4
IMU_INT7: TP155.1, U16.9
IMU_INT8: TP156.1, U16.4
IMU_INT9: TP194.1, U21.9
IMU_INT10: TP195.1, U21.4
IMU_INT11: TP233.1, U26.9
IMU_INT12: TP234.1, U26.4
MOT_3+: J3.1, TP25.1, U5.4
MOT_3+1: J2.1, TP64.1, U7.4
MOT_3+2: J23.1, TP103.1, U12.4
MOT_3+3: J34.1, TP142.1, U17.4
MOT_3+4: J45.1, TP181.1, U22.4
MOT_3+5: J56.1, TP220.1, U27.4
MOT_3-: J3.2, TP26.1, U5.5
MOT_3-1: J2.2, TP65.1, U7.5
MOT_3-2: J23.2, TP104.1, U12.5
MOT_3-3: J34.2, TP143.1, U17.5
MOT_3-4: J45.2, TP182.1, U22.5
MOT_3-5: J56.2, TP221.1, U27.5
MOT_4+: J6.1, TP29.1, U6.2
MOT_4+1: J15.1, TP68.1, U8.2
MOT_4+2: J26.1, TP107.1, U13.2
MOT_4+3: J37.1, TP146.1, U18.2
MOT_4+4: J48.1, TP185.1, U23.2
MOT_4+5: J59.1, TP224.1, U28.2
MOT_4-: J6.2, TP31.1, U6.3
MOT_4-1: J15.2, TP70.1, U8.3
MOT_4-2: J26.2, TP109.1, U13.3
MOT_4-3: J37.2, TP148.1, U18.3
MOT_4-4: J48.2, TP187.1, U23.3
MOT_4-5: J59.2, TP226.1, U28.3
MOT_L+: J4.1, TP27.1, U5.2
MOT_L+1: J10.1, TP66.1, U7.2
MOT_L+2: J24.1, TP105.1, U12.2
MOT_L+3: J35.1, TP144.1, U17.2
MOT_L+4: J46.1, TP183.1, U22.2
MOT_L+5: J57.1, TP222.1, U27.2
MOT_L-: J4.2, TP28.1, U5.3
MOT_L-1: J10.2, TP67.1, U7.3
MOT_L-2: J24.2, TP106.1, U12.3
MOT_L-3: J35.2, TP145.1, U17.3
MOT_L-4: J46.2, TP184.1, U22.3
MOT_L-5: J57.2, TP223.1, U27.3
MOT_R+: J5.1, TP30.1, U6.4
MOT_R+1: J11.1, TP69.1, U8.4
MOT_R+2: J25.1, TP108.1, U13.4
MOT_R+3: J36.1, TP147.1, U18.4
MOT_R+4: J47.1, TP186.1, U23.4
MOT_R+5: J58.1, TP225.1, U28.4
MOT_R-: J5.2, TP32.1, U6.5
MOT_R-1: J11.2, TP71.1, U8.5
MOT_R-2: J25.2, TP110.1, U13.5
MOT_R-3: J36.2, TP149.1, U18.5
MOT_R-4: J47.2, TP188.1, U23.5
MOT_R-5: J58.2, TP227.1, U28.5
unnamed: D1.C, R8.2
unnamed: IMU_ADR.1, R3.2, U4.1
unnamed: I2C.3, R1.2
unnamed: I2C.1, R2.1
unnamed: C10.1, U2.P$6
unnamed: Q1.2, Q1.5, Q1.6, R6.2
unnamed: Q1.3, Q3.1, R10.2
unnamed: F1.1, Q6.3
unnamed: U1.40, VUSB.2
unnamed: R8.1, SYS_PWR.2
unnamed: Q2.2, Q2.5, Q2.6, R9.2
unnamed: R15.2, R16.1, VIN_MEAS.2
unnamed: MOT_MODE_L/3.1, U5.11
unnamed: MOT_MODE_R/4.1, U6.11
unnamed: Q6.1, R12.1, R13.2
unnamed: Q2.3, Q4.1, R11.2
unnamed: C15.1, R17.1, USER.3, USER.4, USER_BTN.1
unnamed: R18.1, R19.1, VUSB.1
unnamed: Q7.2, Q7.5, Q7.6, R7.2
unnamed: Q5.1, Q7.3, R14.2
unnamed: D2.C, R20.2
unnamed: MOT_PWR.2, R20.1
unnamed: D3.C, R21.2
unnamed: R21.1, SYS_PWR1.2
unnamed: MOT_MODE_L/1.1, U7.11
unnamed: MOT_MODE_R/1.1, U8.11
unnamed: IMU_ADR1.1, R24.2, U3.1
unnamed: I2C1.3, R22.2
unnamed: I2C1.1, R23.1
unnamed: C25.1, U9.P$6
unnamed: Q10.2, Q10.5, Q10.6, R27.2
unnamed: Q8.1, Q10.3, R29.2
unnamed: Q11.2, Q11.5, Q11.6, R28.2
unnamed: Q9.1, Q11.3, R30.2
unnamed: Q12.1, R31.1, R32.2
unnamed: F2.1, Q12.3
unnamed: Q14.2, Q14.5, Q14.6, R33.2
unnamed: Q13.1, Q14.3, R34.2
unnamed: R35.1, R36.2, VIN_MEAS1.2
unnamed: C30.1, R37.1, USER1.3, USER1.4, USER_BTN1.1
unnamed: U10.40, VUSB1.2
unnamed: R38.1, R39.1, VUSB1.1
unnamed: D4.C, R40.2
unnamed: MOT_PWR1.2, R40.1
unnamed: D5.C, R41.2
unnamed: R41.1, SYS_PWR2.2
unnamed: MOT_MODE_L/2.1, U12.11
unnamed: MOT_MODE_R/2.1, U13.11
unnamed: IMU_ADR2.1, R44.2, U11.1
unnamed: I2C2.3, R42.2
unnamed: I2C2.1, R43.1
unnamed: C40.1, U14.P$6
unnamed: Q17.2, Q17.5, Q17.6, R47.2
unnamed: Q15.1, Q17.3, R49.2
unnamed: Q18.2, Q18.5, Q18.6, R48.2
unnamed: Q16.1, Q18.3, R50.2
unnamed: Q19.1, R51.1, R52.2
unnamed: F3.1, Q19.3
unnamed: Q21.2, Q21.5, Q21.6, R53.2
unnamed: Q20.1, Q21.3, R54.2
unnamed: R55.1, R56.2, VIN_MEAS2.2
unnamed: C45.1, R57.1, USER2.3, USER2.4, USER_BTN2.1
unnamed: U15.40, VUSB2.2
unnamed: R58.1, R59.1, VUSB2.1
unnamed: D6.C, R60.2
unnamed: MOT_PWR2.2, R60.1
unnamed: D7.C, R61.2
unnamed: R61.1, SYS_PWR3.2
unnamed: MOT_MODE_L/4.1, U17.11
unnamed: MOT_MODE_R/3.1, U18.11
unnamed: IMU_ADR3.1, R64.2, U16.1
unnamed: I2C3.3, R62.2
unnamed: I2C3.1, R63.1
unnamed: C55.1, U19.P$6
unnamed: Q24.2, Q24.5, Q24.6, R67.2
unnamed: Q22.1, Q24.3, R69.2
unnamed: Q25.2, Q25.5, Q25.6, R68.2
unnamed: Q23.1, Q25.3, R70.2
unnamed: Q26.1, R71.1, R72.2
unnamed: F4.1, Q26.3
unnamed: Q28.2, Q28.5, Q28.6, R73.2
unnamed: Q27.1, Q28.3, R74.2
unnamed: R75.1, R76.2, VIN_MEAS3.2
unnamed: C60.1, R77.1, USER3.3, USER3.4, USER_BTN3.1
unnamed: U20.40, VUSB3.2
unnamed: R78.1, R79.1, VUSB3.1
unnamed: D8.C, R80.2
unnamed: MOT_PWR3.2, R80.1
unnamed: D9.C, R81.2
unnamed: R81.1, SYS_PWR4.2
unnamed: MOT_MODE_L/5.1, U22.11
unnamed: MOT_MODE_R/5.1, U23.11
unnamed: IMU_ADR4.1, R84.2, U21.1
unnamed: I2C4.3, R82.2
unnamed: I2C4.1, R83.1
unnamed: C70.1, U24.P$6
unnamed: Q31.2, Q31.5, Q31.6, R87.2
unnamed: Q29.1, Q31.3, R89.2
unnamed: Q32.2, Q32.5, Q32.6, R88.2
unnamed: Q30.1, Q32.3, R90.2
unnamed: Q33.1, R91.1, R92.2
unnamed: F5.1, Q33.3
unnamed: Q35.2, Q35.5, Q35.6, R93.2
unnamed: Q34.1, Q35.3, R94.2
unnamed: R95.1, R96.2, VIN_MEAS4.2
unnamed: C75.1, R97.1, USER4.3, USER4.4, USER_BTN4.1
unnamed: U25.40, VUSB4.2
unnamed: R98.1, R99.1, VUSB4.1
unnamed: D10.C, R100.2
unnamed: MOT_PWR4.2, R100.1
unnamed: D11.C, R101.2
unnamed: R101.1, SYS_PWR5.2
unnamed: MOT_MODE_L/6.1, U27.11
unnamed: MOT_MODE_R/6.1, U28.11
unnamed: IMU_ADR5.1, R104.2, U26.1
unnamed: I2C5.3, R102.2
unnamed: I2C5.1, R103.1
unnamed: C85.1, U29.P$6
unnamed: Q38.2, Q38.5, Q38.6, R107.2
unnamed: Q36.1, Q38.3, R109.2
unnamed: Q39.2, Q39.5, Q39.6, R108.2
unnamed: Q37.1, Q39.3, R110.2
unnamed: Q40.1, R111.1, R112.2
unnamed: F6.1, Q40.3
unnamed: Q42.2, Q42.5, Q42.6, R113.2
unnamed: Q41.1, Q42.3, R114.2
unnamed: R115.1, R116.2, VIN_MEAS5.2
unnamed: C90.1, R117.1, USER5.3, USER5.4, USER_BTN5.1
unnamed: U30.40, VUSB5.2
unnamed: R118.1, R119.1, VUSB5.1
unnamed: D12.C, R120.2
unnamed: MOT_PWR5.2, R120.1
RP_IO0/ENC_3_A: J3.4, TP1.1, U1.1
RP_IO0/ENC_3_A1: J2.4, TP40.1, U10.1
RP_IO0/ENC_3_A2: J23.4, TP79.1, U15.1
RP_IO0/ENC_3_A3: J34.4, TP118.1, U20.1
RP_IO0/ENC_3_A4: J45.4, TP157.1, U25.1
RP_IO0/ENC_3_A5: J56.4, TP196.1, U30.1
RP_IO1/ENC_3_B: J3.5, TP2.1, U1.2
RP_IO1/ENC_3_B1: J2.5, TP41.1, U10.2
RP_IO1/ENC_3_B2: J23.5, TP80.1, U15.2
RP_IO1/ENC_3_B3: J34.5, TP119.1, U20.2
RP_IO1/ENC_3_B4: J45.5, TP158.1, U25.2
RP_IO1/ENC_3_B5: J56.5, TP197.1, U30.2
RP_IO2/MOT_3_PH: TP3.1, U1.4, U5.8
RP_IO2/MOT_3_PH1: TP42.1, U7.8, U10.4
RP_IO2/MOT_3_PH2: TP81.1, U12.8, U15.4
RP_IO2/MOT_3_PH3: TP120.1, U17.8, U20.4
RP_IO2/MOT_3_PH4: TP159.1, U22.8, U25.4
RP_IO2/MOT_3_PH5: TP198.1, U27.8, U30.4
RP_IO3/MOT_3_EN: TP4.1, U1.5, U5.7
RP_IO3/MOT_3_EN1: TP43.1, U7.7, U10.5
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

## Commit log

2023-01-18 Create Pico W library file
2023-01-18 Add initial schematic and board layout
    [XRP_Controller.brd, XRP_Controller.sch]
2023-01-18 Clean up schematic
    Add dashed lines between regions
    Add I2C address for IMU
    Add max voltages for motor drivers, 5V regulator, and Pico W
    Rename jumpers and indicate functions
    [XRP_Controller.brd, XRP_Controller.sch]
2023-01-19 Design review updates
    Replace 2 power switch FETs with 1 at output of perfect diodes
    Add perfect diode to make Pico's VSYS be input only
    Extend board length to 2.125in
    Move reset button away from edge, to center of left side
    Swap right side motor IO pins
    Rename connectors and corresponding nets
    Change connector label silk to match
    [XRP_Controller.brd, XRP_Controller.sch]
2023-01-19 Design review updates
    Add debounce capacitor to reset button
    Increase power trace widths to 25 mils
    Pull 5V polygon out from under inductor and add GND vias
    [XRP_Controller.brd, XRP_Controller.sch]
2023-01-19 Design review updates
    Add silk lines between adjacent passive components
    Rename "!EN!" net to "!POW_EN!"
    Add text next to power switch indicating function
    [XRP_Controller.brd, XRP_Controller.sch]
2023-01-20 Design review updates
    Pico footprint:
    Change pad and paste geometry based on DFM feedback (no copper or paste under the inner holes of the Pico's pads), and over paste outside of pads for better fillets)
    Reduce paste under test points
    Remove paste from USB PTH pads
    Schematic:
    Nudge power MOSFET to prevent !POW_EN! flag from overlapping net
    Remove "32V max" from 5V buck to avoid confusion with 11V max for VIN
    Board:
    Improve GND continuity
    Add test points for 5V buck EN and PG
    Fix motor connector silk labels
    Remove acid traps at encoder pins
    Approve erroneous DRC errors
    [XRP_Controller.brd, XRP_Controller.sch]
2023-01-25 Add proto production files
    [XRP_Controller-Panel.GBL, XRP_Controller-Panel.GBO, XRP_Controller-Panel.GBP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]
2023-01-30 v02 updates
    Bump version number
    Add tKeepout, tName and tValue to Pico W footprint
    Reorganize schematic
    Change servo header to locking footprint
    Add test points for all GPIO pins
    Add inverted Qwiic logo
    Add selective solder paths to layer 48
    Add barrel polarity silk to bottom
    Add PTH silk labels to bottom
    Add axes silk to bottom
    [XRP_Controller.brd, XRP_Controller.sch]
2023-02-13 Update Pico W footprint tDocu
    Now with more accurate pad geometry!
    [XRP_Controller.brd, XRP_Controller.sch]
2023-02-13 Update buck footprint with reduced paste
    [XRP_Controller.brd, XRP_Controller.sch]
2023-02-13 Nudge servo silk to improve readability
    [XRP_Controller.brd]
2023-03-01 Design review updates
    Move version number in schematic to correct location
    Rename 2nd expansion connector from "Range" to "Extra"
    Rename 4th expansion connector from "Conn4" to "Range"
    Add VIN measurement through voltage divider and NC jumper to IO28
    Add V_BATT test point
    [XRP_Controller.brd, XRP_Controller.sch]
2023-03-06 Design review updates
    Restore Q6 value
    Add user button to IO22 via NC jumper
    Move USB_POW next to Pico W
    Add current limiting resistor to VUSB
    Place user button at top left corner
    Move USB_POW jumper under barrel connector
    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
    [XRP_Controller.brd, XRP_Controller.sch]
2023-03-15 v10 updates
    Bump version number to v10
    Update Pico W datasheet
    Change Pico W footprint to match datasheet recommendations
    Nudge inner expansion connectors inwards to be on 0.05" grid
    Rename USB_POW jumper to VUSB
    Replace PWR_LED jumper silk label with PWR
    Add XRP logos
    [XRP_Controller.brd, XRP_Controller.sch]
2023-03-15 Minor routing improvments
    Nudge a couple traces to improve GND continuity
    [XRP_Controller.brd]
2023-03-17 Update VUSB path
    Replace R18 with 2x 1206 10 Ohm resistors in parallel (better power rating than a single 0603)
    Change VUSB jumper from NO to NC
    Flip 3V3 and VBUS pins of Pico W footprint
    [XRP_Controller.brd, XRP_Controller.sch]
2023-03-17 Design review updates
    Add IO22 silk label to user button
    Move VUSB jumper under V_SYS label in schematic
    Renumber last few test points
    Add test point for IMU interrupt pin
    [XRP_Controller.brd, XRP_Controller.sch]
2023-03-17 Minor tweaks
    Nudge C3 to be on grid
    Move MOT_3_EN via to not overlap with RESET silk
    Nudge V_SYS trace and reduce width to get better GND pour
    [XRP_Controller.brd]
2023-03-17 Fix "Range" silk
    Modify the Buzzard footprint to have a lower bottom edge
    [XRP_Controller.brd]
2023-03-20 Connect SCX pin of IMU to GND
    Datasheet says to do this, whoops!
    Pins 10-12 have internal pullups, can leave unconnected
    [XRP_Controller.brd, XRP_Controller.sch]
2023-03-20 Put all XRP specific parts into a single library
    Helps ensure PROD_ID values are correct for this project
    [XRP_Controller.brd, XRP_Controller.sch]
2023-03-20 Update RP2040 and IMU datasheets
2023-03-21 Nudge vias to clean up silk text
    [XRP_Controller.brd]
2023-03-21 Minor tweaks
    Nudge I2C jumper back onto grid
    Nudge a couple power traces under Pico W
    [XRP_Controller.brd]
2023-03-22 Design review updates
    Motor mode jumpers - add "/3" and "/4" to jumper names
    Overlay copper version number with silk version number
    Change IMU_ADR jumper from NO to NC, and swap with R3 to keep same default address
    Add second power LED to indicate motor power vs system power
    Change power LEDs to DIO-17976 and corresponding resistor values
    [XRP_Controller.brd, XRP_Controller.sch]
2023-03-23 Put OSHW logo back onto board
    [XRP_Controller.brd]
2023-03-31 Add OpenSTEM logos
    [XRP_Controller.brd]
2023-03-31 Add inverted Qwiic logo as library part
    [XRP_Controller.brd, XRP_Controller.sch]
2023-03-31 v09 tweaks
    Ordering a few boards early before logos are finalized
    Removed URLs for now
    [XRP_Controller.brd, XRP_Controller.sch]
2023-03-31 Add v09 panel files
    [XRP_Controller-Panel.GBL, XRP_Controller-Panel.GBO, XRP_Controller-Panel.GBS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]
2023-04-07 v10 updates
    Remove OpenSTEM logo
    Add XRP URL to top and bottom silk
    Nudge expansion connectors in schematic to not have overlapping labels
    Nudge Qwiic logo to get thicker silk along bottom edge
    Approve DRC overlap errors
    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
    [XRP_Controller.brd, XRP_Controller.sch]
2023-04-14 Minor tweaks
    Update buck footprint to link to SFE Eagle library
    Change motor nets and silk labels to use +/- instead of P/N
    [XRP_Controller.brd, XRP_Controller.sch]
2023-04-14 Add ordering instructions
    [XRP_Controller.brd]
2023-04-14 Add v10 panel files
    [XRP_Controller-Panel.GBL, XRP_Controller-Panel.GBO, XRP_Controller-Panel.GBS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]
2023-04-25 Move user button
    Corner was not accessible enough in chassis. User button now takes the location of the XRP logo just under the SparkFun logo
    [XRP_Controller.brd]
2023-04-25 Fix GND flow
    [XRP_Controller.brd]
2023-04-25 Add motor IO silk to top corners
    Also remove extra via under user button
    [XRP_Controller.brd]
2023-04-27 Add silk lines between power LEDs and resistors
    [XRP_Controller.brd]
2023-04-27 Update v10 panel files
    [XRP_Controller-Panel.brd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]
2023-06-15 Update Pico W with more paste on castellated pads
    Turns out the Pico W boards are slightly warped (about 100um), meaning pads at the ends are frequently not connected. More paste should help!
    [XRP_Controller-Panel.brd, XRP_Controller.brd, XRP_Controller.sch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]
2023-06-27 Updating Buttons desc
    Updating buttons description to include BOOTSEL button. New photo highlighting BOOTSEL button.
2023-09-07 Moved components to SFE Eagle libraries
    [XRP_Controller.brd, XRP_Controller.sch]
2025-02-25 Update product names & yml files
    Updating Hardware Overview & Resources documents with current XRP Beta product names. Updating main and workflows .yml files to current version.
2025-03-13 XRP Release Update
    Creating merge branch for review before merging with main. This includes all files for updated documentation and adding hardware/production files for XRP "non-beta". File and folder movement and crea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
    [SparkFun_XRP_Controller.kicad_sch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]
2025-03-13 Re-organize hardware files
    [SparkFun_XRP_Controller.kicad_sch, XRP_Controller_Beta.brd, XRP_Controller_Beta.sch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]
2025-03-13 Re-organize production files
    [SparkFun_XRP_Controller_panelized.GBL, SparkFun_XRP_Controller_panelized.GBS, SparkFun_XRP_Controller_panelized.GKO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]
2025-03-13 Fix ordering instructions and add .drl file
    [SparkFun_XRP_Controller_panelized.drl]
2025-03-17 Update XRP KiCad ZIP
    Updating XRP Controller KiCad ZIP folder with the correct files.
2025-03-20 Update resources.md
    added new 3D printing files - Sean
2026-06-08 Update hardware_overview.md
    Updating barrel jack voltage range to clarify use of alternate battery types.

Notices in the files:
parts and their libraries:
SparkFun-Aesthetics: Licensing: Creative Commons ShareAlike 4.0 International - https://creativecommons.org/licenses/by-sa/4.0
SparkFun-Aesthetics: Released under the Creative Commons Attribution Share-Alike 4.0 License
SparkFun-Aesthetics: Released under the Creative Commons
